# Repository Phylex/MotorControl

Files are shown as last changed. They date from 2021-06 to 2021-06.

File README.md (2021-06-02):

MotorControl
============
This Repository has the Kicad source files for an H-Bridge that I want to use in my model RC Boats.
It is based around the DRV8701P H-Bridge driver Chip.

It's used in conjunction with Infineon IDP060N03L-G Mosfets with an Rd-on of 6 mOhm, so they should be good up to around 40-50 Amps.

Features
--------
It's main Features are: 
1. Current measurement via a Shunt resistor.

2. Reverse polarity protection. 

3. A settable maximum current (courtesy of current chopping of the DRV8701)

4. The input current is smoothed via an inductor/capacitor combination of 2.2uH/440uF respectively.

5. A maxixum operating PWM frequency of 50 kHz.

Notes
-----
1. According to my calculations and the voltage that is likely to power the Boats (2S Li-Ion battery packs) the maxixum PWM frequency that the charge pump
of the DRV8701P supports is 86kHz so far outside the problematic resonance frequency of 5.1 kHz of the Inductor/Capacitor current smoothing

2. The total gate charge of one MOSFET is < 14.4 nC which is roughly the number that the reference design in the Data sheet mentions.
In this case The current source for the high-side FETs is set to 100mA via a resistor on the board. This gives the FETs a worst case rise time of 144
ns.

3. The Resonance of the Inductor-Capacitor circuit is at roughly 5.1 kHz, so A PWM frequency a fair bit higher is recommended.)

4. The data sheet mentions a maxixum current chopping frequency of 38 kHz so well inside the maximum supported frequency.

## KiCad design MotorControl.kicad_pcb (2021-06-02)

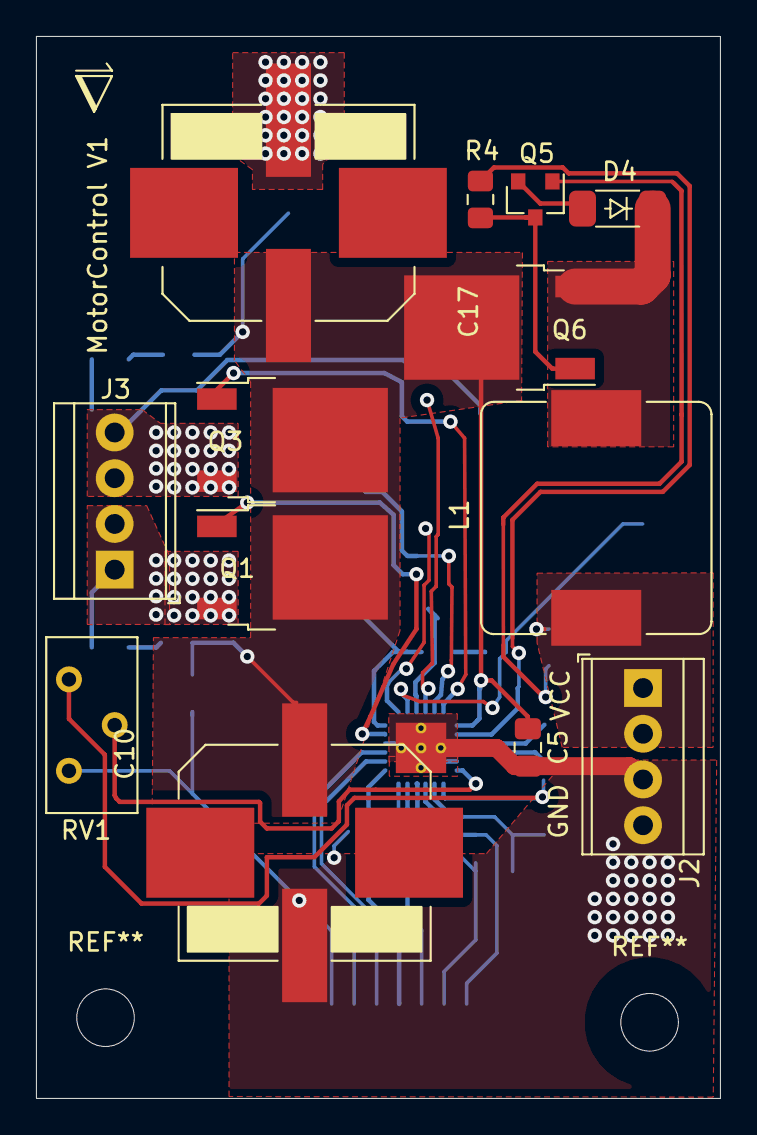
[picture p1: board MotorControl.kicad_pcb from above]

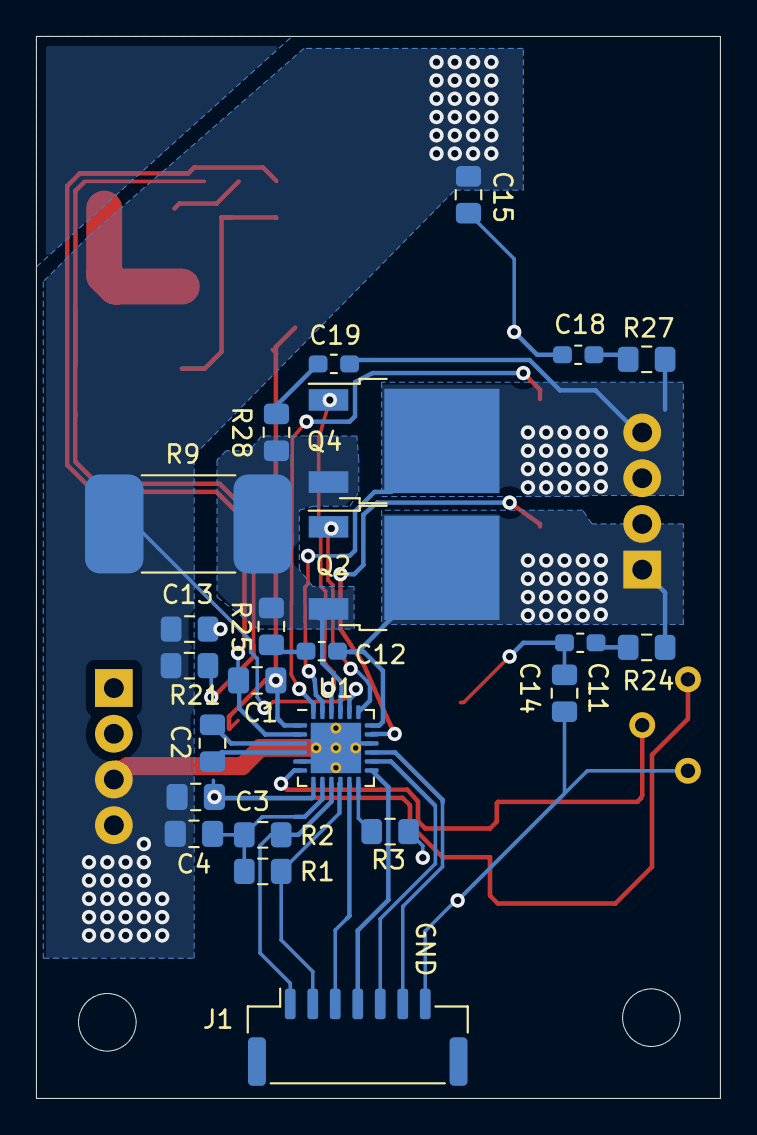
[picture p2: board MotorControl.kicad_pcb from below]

Board: 2 copper layers, 38.0 x 59.0 mm, 37 parts (24 on the bottom side), 31 nets.

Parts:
C1, C3, C4: 1uF; C_0805_2012Metric_Pad1.18x1.45mm_HandSolder
C2: 100nF; C_0805_2012Metric_Pad1.15x1.40mm_HandSolder
C5: 100nF; C_0805_2012Metric_Pad1.18x1.45mm_HandSolder
C10, C17: 220uf; Vishay_ELKO_1213
C11, C12, C18, C19: 4.7n; C_0603_1608Metric_Pad1.05x0.95mm_HandSolder
C13: 100n; C_0805_2012Metric_Pad1.15x1.40mm_HandSolder
C14, C15: 2.2uF; C_0805_2012Metric_Pad1.15x1.40mm_HandSolder
D4: BZT55C12; MELF_SOD-80
J1: Conn_01x07_Female; JST_GH_SM07B-GHS-TB_1x07-1MP_P1.25mm_Horizontal
J2, J3: Screw_Terminal_01x04; TerminalBlock_TE_282834-4_1x04_P2.54mm_Horizontal
L1: 2.2uH; L_Bourns_SRP1245A
Q1, Q2, Q3, Q4, Q6: IPD060N03L G; TO-252-2
Q5: BC846B,215; SOT-23
R1, R2, R4: 10K; R_0805_2012Metric_Pad1.15x1.40mm_HandSolder
R3: 1G; R_0805_2012Metric_Pad1.15x1.40mm_HandSolder
R9: 3m; TE_LRS1050
R21: 47k; R_0805_2012Metric_Pad1.15x1.40mm_HandSolder
R24, R25, R27, R28: 2; R_0805_2012Metric_Pad1.15x1.40mm_HandSolder
RV1: 200K; Potentiometer_Bourns_3386X_Horizontal
U1: DRV8701P; QFN-24-1EP_4x4mm_P0.5mm_EP2.8x2.8mm_ThermalVias

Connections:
/AVDD: C3.1, RV1.1, U1.7
/DVDD: C4.1, R1.1, R2.1, U1.8
/GH1: Q1.1, U1.17
/GH2: Q3.1, U1.24
/GL1: Q2.1, U1.19
/GL2: Q4.1, U1.22
/IN1: J1.6, U1.15
/IN2: J1.5, U1.14
/MOTL: C12.1, J3.1, J3.2, Q1.3, Q2.2, R24.2, U1.18
/MOTR: C19.1, J3.3, J3.4, Q3.3, Q4.2, R27.2, U1.23
/SL: Q2.3, Q4.3, R9.2, R25.2, R28.2, U1.21
/SNSOUT: J1.2, R1.2, U1.10
/SO: J1.3, U1.11
/nFAULT: J1.1, R2.2, U1.9
/nSLEEP: J1.4, U1.13
GND: C3.2, C4.2, C5.2, C10.2, C13.2, C14.2, C15.1, C17.2, J1.7, J2.3, J2.4, R3.2, R9.1, R21.2, RV1.3, U1.5, U1.16, U1.20, U1.25
unnamed: C1.1, R4.2, U1.2
unnamed: C1.2, C5.1, C10.1, C11.1, C14.1, C15.2, C17.1, C18.1, Q1.2, Q3.2, Q6.2, U1.1
unnamed: C2.1, U1.3
unnamed: C2.2, U1.4
unnamed: C11.2, R24.1
unnamed: C12.2, R25.1
unnamed: C18.2, R27.1
unnamed: C19.2, R28.1
unnamed: D4.1, L1.2, Q6.3
unnamed: D4.2, Q5.2
unnamed: Q5.1, R21.1
unnamed: Q5.3, Q6.1, R4.1
unnamed: R3.1, U1.12
unnamed: RV1.2, U1.6
VPP: C13.1, J2.1, J2.2, L1.1
